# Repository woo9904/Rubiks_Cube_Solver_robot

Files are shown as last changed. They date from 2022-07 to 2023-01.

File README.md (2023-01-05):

# Rubiks Cube Solver Ver. 1.0 (RCSv1)

My first robot use Raspberry Pi 4 and Dynamixel_servo_motor(XM430-W350-T).   
It also detect 6 sides of the Rubiks_Cube and solving it with servo_motor.   
What i use algorithm is image precessing, motor control and python thread for LCD.   

In this code i modified cube detection algorithm, motor control and i added LCD.

임베디드장비(Raspberry Pi 4 B+)와 영상처리(큐브 인식), Dynamixel 제어를 스스로 공부해보고 활용해 큐브를 자동으로 맞춰주는 로봇을 만들었다.   
추가적으로 결과물 입출력을 확인하기 위해서 LCD패널 및 다양한 외부회로를 만들었다.   

* **제작자 : 정우진(Woo)**
* **제작 기간 : 22.02.28~22.05.15**
* **보고서 작성 일 : 22.05.25**

I reference this link. (Thank you Andrea Favero, Groningen(NL) for giving source.)
* [Reference_link](https://www.instructables.com/Rubik-Cube-Solver-Robot-With-Raspberry-Pi-and-Pica/)   

## Description

22년 5월 15일 최종적으로 1차 제작 완료한 모델로,
무작위로 섞은 큐브를 PiCam으로 인식하고, Dynamixel을 사용해 큐브를 푸는 로봇이다. 

큐브를 인식하고 푸는 시간은 총 3분 10초에서 3분 30초가 걸린다.   
빠른 로봇은 아니고, 이미 만들어진 제품을 참고한 작품이지만 스스로 배우고 학습하기에 적합한 활동이었다.  
이후 동아리 후배들이 작품을 봤을 때 자극을 받아 더 발전할 것이다.   
추후에는 더 발전시켜 완성도를 높일 것이다.

위 영상은 작동과정을 보여주고 있는 영상으로, 2배속을 한 영상이다.    
Video Label (https://youtu.be/7SincwjlR4I)

## Environment
실행에 필요한 package이다.   
* Hardware

로봇을 만드는데 사용한 부품에 대해 적는다.
|Raspberry Pi 4 Model B 4GB | Raspberry Pi Camera V2 | Dynamixel XM430-W350-T | U2D2 | GANCUBE | 
|--|--|--|--|--|
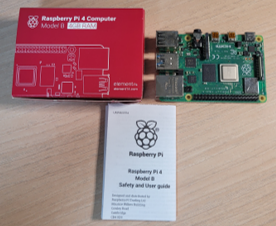
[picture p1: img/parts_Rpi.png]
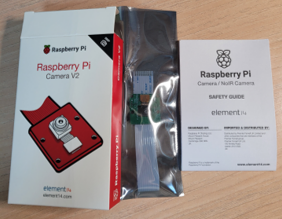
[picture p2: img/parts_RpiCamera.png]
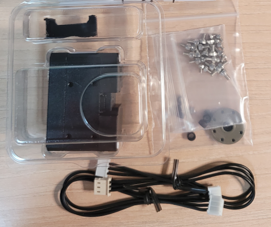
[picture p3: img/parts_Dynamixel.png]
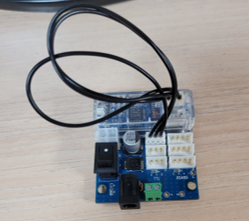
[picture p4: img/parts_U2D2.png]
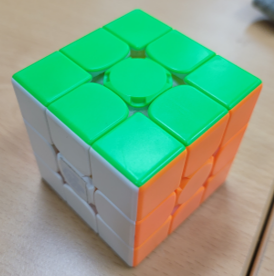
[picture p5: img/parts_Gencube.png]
||||||

* 3D models

각각 부품들을 조합해 나타낸 것이다. 세부 부품 설명은 추후에 적겠다. 
|3d model|출력 및 조립|
|---|---|
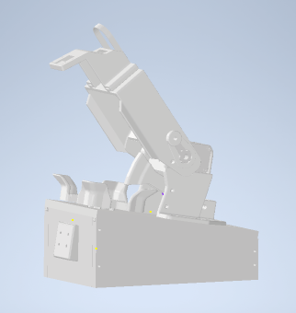
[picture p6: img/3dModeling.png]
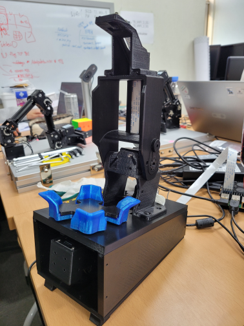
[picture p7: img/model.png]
|||

* Software

  * python 3.7.3, cv2 4.1.2
  * numpy, RPi.GPIO, PiCamera
  * twophase.solver (to install `$ pip install RubikTwoPhase`) 
  * Dynamixel_SDK (to install [link](https://emanual.robotis.com/docs/en/software/dynamixel/dynamixel_sdk/download/#repository))
  
## Files
작성한 코드가 각자 어떤 역할을 하는지 설명해준다. 
1. cube_detect_pi.py
    * 큐브 인식하기 위한 알고리즘
	* 이미지 프로세싱 포함
	
2. gpio_control.py
    * LCD화면, LED 등 외부 회로를 제어하기 위한 코드
	* 쓰레드를 사용함
	
3. main.py
    * 전체적인 코드를 통합한 코드
	* 각 코드를 연결하기 위한 코드이다. (main)
	
4. motor_control.py
    * 모터를 제어하기 위한 코드
	* 3개의 모터를 제어해 큐브를 돌린다.

추가적으로 motor제어에 안정화를 위해서 "Dynamixel_SDK"의 다음 라이브러리를 수정했다. 
-> 어떤 내용인지 작성하기

## Usage
작품을 실행하기 위한 방법에 대해 설명한다. 
1. Environment를 참고해 3d 모델을 뽑아 조립한다.
2. 그후 Hardware을 연결한다.
3. Software을 참고해 Raspberry Pi의 환경 세팅한다. 
4. git clone을 통해 CODE 부분을 Raspberry Pi에 저장한다. 
5. 명령창을 CODE의 폴더로 이동해 다음과 같이 명령어를 입력한다. 
```
$ python3 main.py
```
6. 그 후 외부 회로를 만들어 (회로도 참고) 버튼을 클릭해 실행한다. 
7. 만든 로봇을 통해 큐브를 맞춘다!

---------------------------------------------------------
## Story(a development journal)
개발 과정에 대해서 설명한다. 

### 개발 동기

필자는 임베디드 시스템을 한번도 경험해 보지 못했다. 이번 기회에 Raspberry Pi에 익숙해지고 경험을 쌓기로 했다.    
또한 모터 제어하는 방법을 잘 알지 못해 눈으로 로봇이 작동하는 것을 확인할 수 있으며 재미를 갖을 수 있는 요소를 찾다가   
'큐브 자동으로 맞춰주는 로봇'을 알게 되었다.    

또한 국민대 자율주행 자동차 대회 참가를 통해 처음 알게 된 image processing 기술을(본선진출) 좀더 이해하고 발전시켜 나가보기로 했다.   

따라서 다음과 같은 이유로 Cube solver을 제작하기로 했다. 

### 개발 목표

1) Picamera를 사용해 Cube 색깔 인식 알고리즘 구현   
2) 주어진 부품(Servo motor : Dynamixel)에 맞출 수 있는 로봇 하드웨어 modeling   
3) Dynamixel SDK를 참고해 모터 동작 알고리즘 구현   
4) 구현한 알고리즘과 하드웨어 결합으로 로봇 만들기   
5) LCD화면 및 스위치 장착   

## 작품 구성

로봇이 어떻게 구성되어 있는지 사진과 설명을 적는다. 또한 각 부품들이 어떤 역할을 하는지 설명한다.

### 작품 전체 사진

전체적인 작품 사진을 찍고 설명한다.
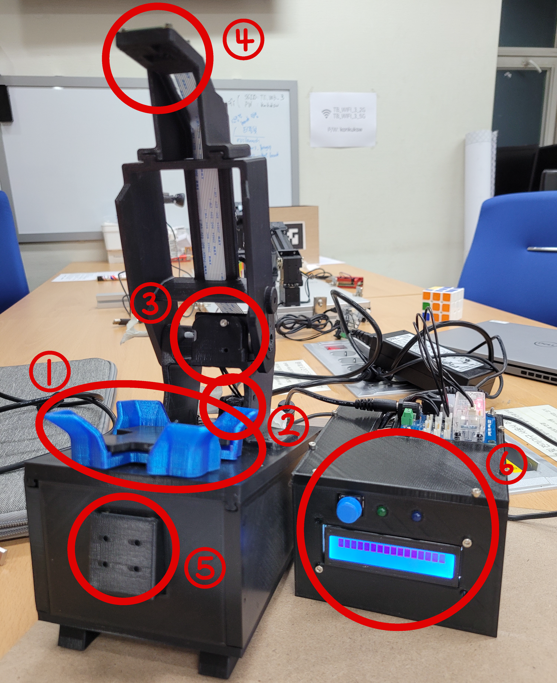
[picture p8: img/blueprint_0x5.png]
title

(시간 문제로 case부분 3d모델링을 하지 못해 임시적으로 사진을 다음과 같이 첨부했습니다.)

사용된 servo motor은 총 3개로 Robotis사의 Dynamixel XM430-W350-T모델을 사용했다.   
사용된 위치는 (1), (2), (3)이다.    

지면과 수평인 부분을 x축, 사진을 바라보고 있는 방향을 y축, 지면과 수직인 방향이 z축이라고 가정할 때,   
지면과 평면(xy축 평면)인 부분으로 회전시켜 주기 위해서 (1)번이 동작해야 하고,   
지면과 수직(yz축 평면)인 부분으로 회전시켜 주기 위해서는 (2)번이 동작해야 한다.   
큐브 면을 회전시키기 위해서는 큐브를 (3)모터로 고정시킨뒤 (1)번 모터를 동작시킨다.   

아래 사진은 2번 모터에서 shift가 동작해 큐브를 뒤집어 주는 모습이다.   
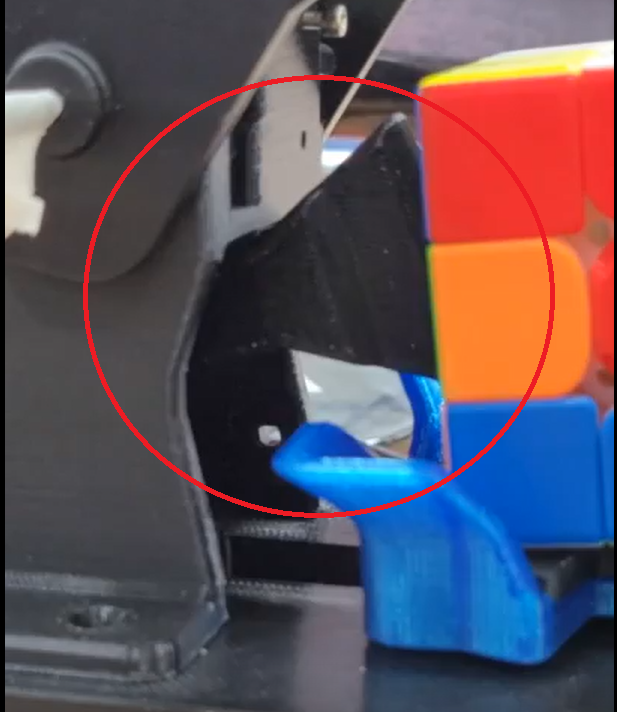
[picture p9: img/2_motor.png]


(4)번은 큐브면을 인식시켜 (color detect) 큐브 맞추는 solution을 제공하기 위해서 Rpi camera를 설치하였다.   
(5)번은 전체적으로 cube solver robot을 축소화 시키면서 발생한 부분이며, (1)번 모터를 고정시키기 위해서 필요한 motor holder이다.   
(6)번은 아직 case 완성품을 만들기 전이며, 외부 회로와 Raspberry pi를 보관하기 위한 case이다.   
motor를 크고 키기 위한 U2D2와 스위치는 보이는 곳에 두었다.   

* 동작 원리

전체적인 동작 원리는   
-> (6)번의 LCD화면을 통해 부팅이 성공적인지 확인 후, 스위치를 눌러 시작   
-> (4)번의 camera를 통해 cube의 6면의 색깔을 모두 인식 (이때 (1), (2), (3), 모터를 모두 사용해 큐브를 인식하기 위해 모터를 동작시킨다.)   
-> 인식된 색깔을 통해 cube solution을 계산하고 (1), (2), (3) 모터를 통해 큐브를 맞추기.   
-> 큐브를 모두 맞춘 경우, LCD화면에 성공 글자를 출력시키고, 다시 초기 상태로 복귀한다. 

### 사용한 부품

로봇을 만드는데 사용한 부품에 대해 적는다.
|Raspberry Pi 4 Model B 4GB | Raspberry Pi Camera V2 | Dynamixel XM430-W350-T | U2D2 | GANCUBE | 
|--|--|--|--|--|
|nn|nn|nn|nn|nn|

### 모델 parts
로봇을 만들기 위한 3D모델링에 대한 설명이다. 
아래 사진은 모델링을 하기 위해 참고한 모델들이다. 

|1번|2번|3번|
|--|--|--|
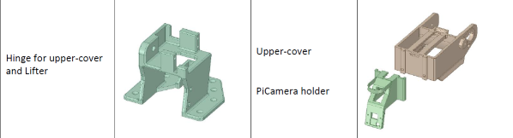
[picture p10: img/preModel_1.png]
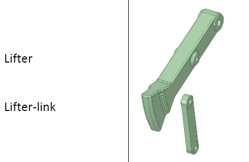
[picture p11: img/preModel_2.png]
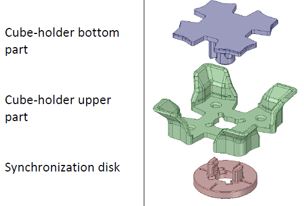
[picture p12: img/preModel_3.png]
||||

하지만 아래 사진 처럼 주어진 모델이 사용하고자 하는 servo motor에 맞지 않았다. 

|1번|2번|3번|
|---|---|---|
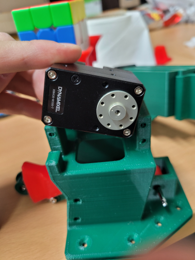
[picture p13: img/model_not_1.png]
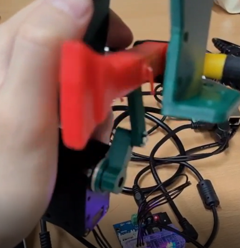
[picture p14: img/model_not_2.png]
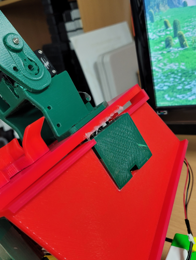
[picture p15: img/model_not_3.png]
||||
|기본 모델이 servo motor 크기와 부합. |Lifter 부분이 motor과 다른 설계로 cube를 뒤집지 못함. | motor을 holder 부분이 없어 부품 조립에 문제. |

3D 모델링으로 모든 모델링을 수정하고 제작해 다음과 같은 모델을 만들 수 있게 되었다. 

|3d model|출력 및 조립|
|---|---|
|nn|nn|

## 작동 알고리즘

로봇이 큐브를 인식하기 부터 풀기까지 모든 동작의 알고리즘에 대해 설명한다. 

### 배경지식

해당 로봇과 관련된 선행 조사에 대해 작성한다.
사용한 큐브   

|western_cube|cube_table|
|--|--|
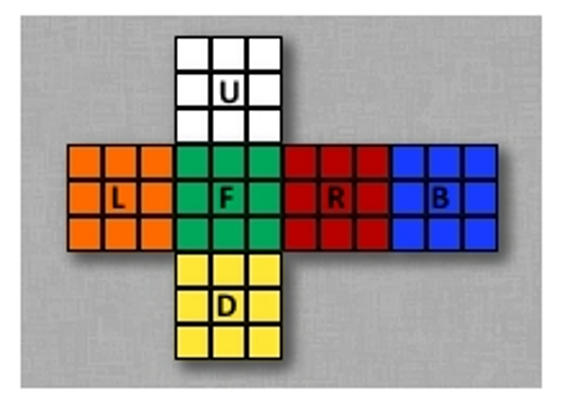
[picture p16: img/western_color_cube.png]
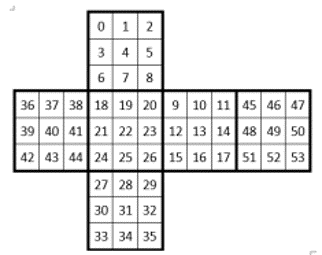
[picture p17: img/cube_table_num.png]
|||

 큐브 설명하기
|큐브 돌릴때 사용하는 명칭| 큐브 맞추는 방법 알고리즘|
|--|--|
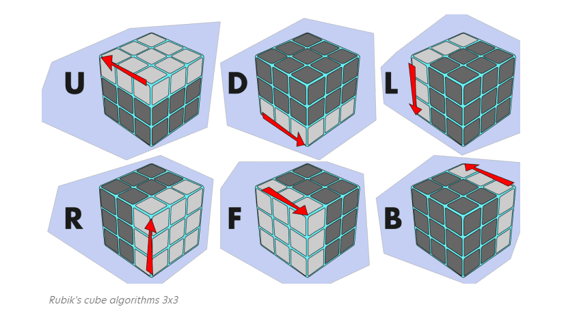
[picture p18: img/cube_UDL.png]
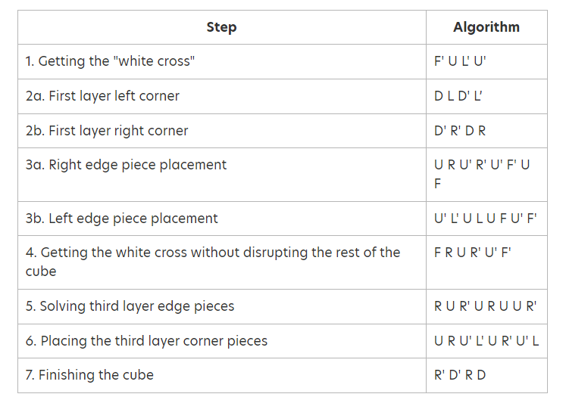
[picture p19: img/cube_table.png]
|||

 Raspberry Pi의 GPIO

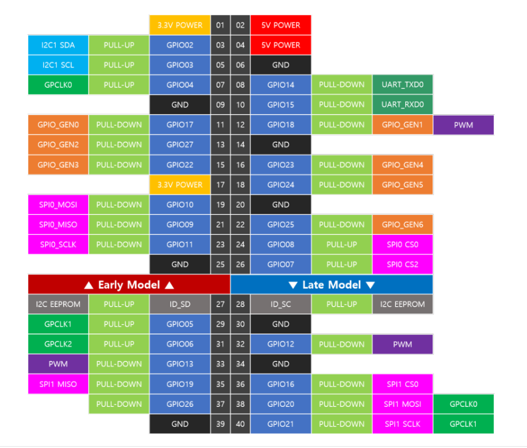
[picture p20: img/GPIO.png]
   

### 사용한 기술

일을 수행하기 위한 사용한 알고리즘 및 기법에 대해 작성한다.

1. OpenCV, cube face contour detect

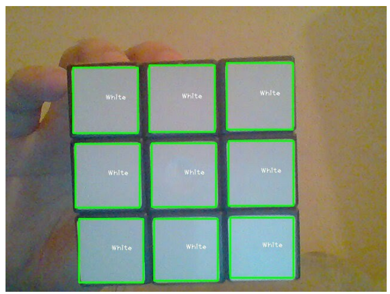
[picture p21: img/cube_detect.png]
   

2. color recognize using HSV

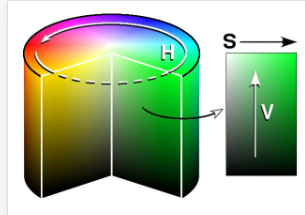
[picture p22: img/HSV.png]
   

3. Dynamixel SDK

## 개발 과정

개발하면서 크게 어려웠던 점을 순서대로 나열하고 해결방법은 아래에 작성한다.

### 하드웨어 개발 과정

### 소프트웨어 개발 과정

#### 영상처리

#### 모터제어

## 추후 목표

## 결론

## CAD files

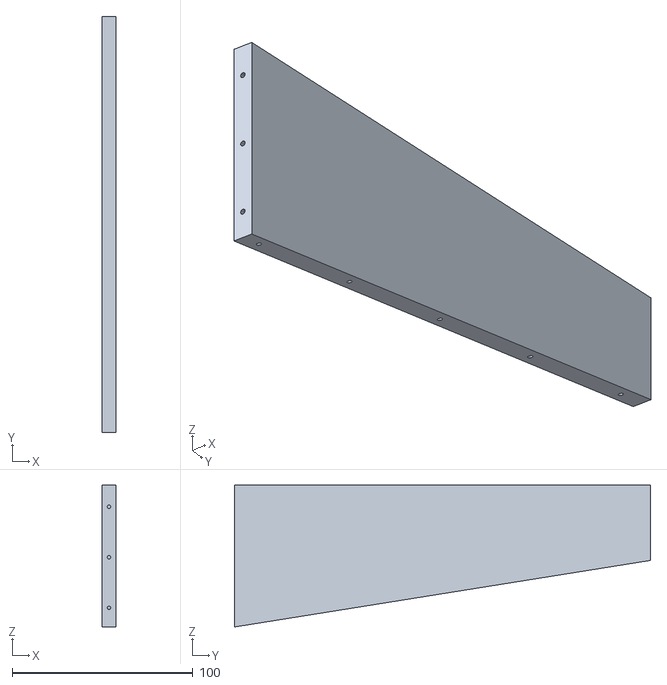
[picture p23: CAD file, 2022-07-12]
3D_model/stl_for_model/Panel_left.stl
8.00 x 230.0 x 78.5

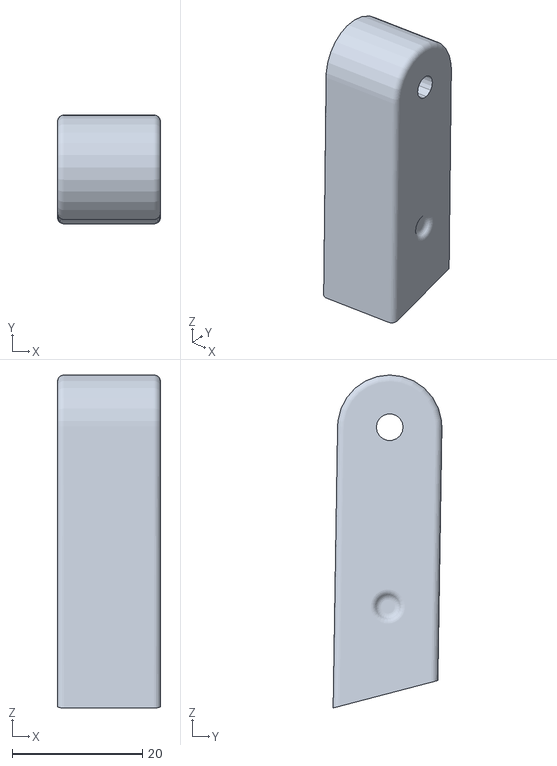
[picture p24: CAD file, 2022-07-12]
3D_model/stl_for_model/Foot.stl
15.8 x 16.7 x 51.0

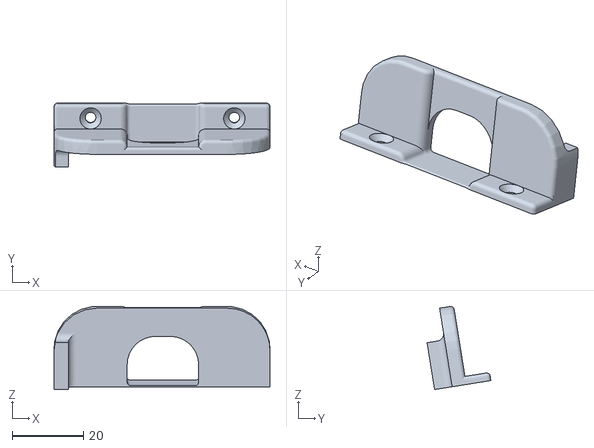
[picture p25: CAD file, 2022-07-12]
3D_model/stl_for_model/Rpi_holder_back.stl
60.5 x 17.9 x 23.3

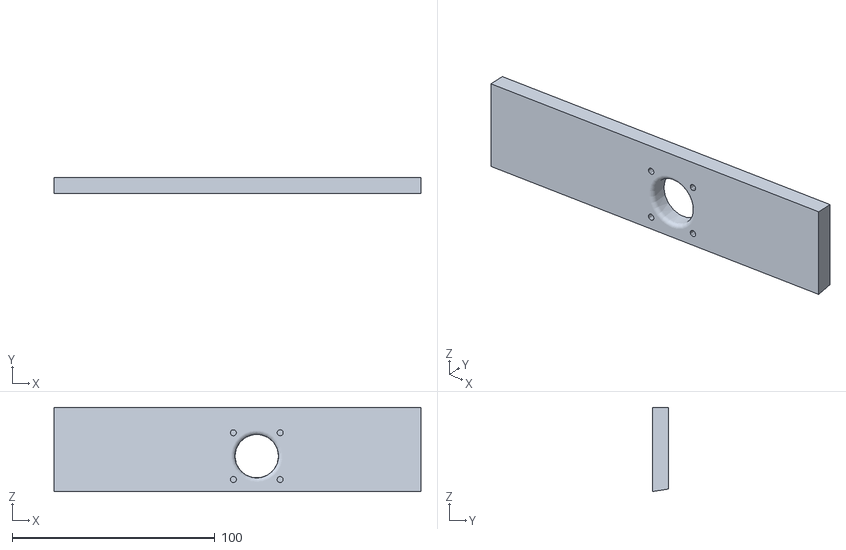
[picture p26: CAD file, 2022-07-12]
3D_model/stl_for_model/Panel_back.stl
181.0 x 8.00 x 41.5

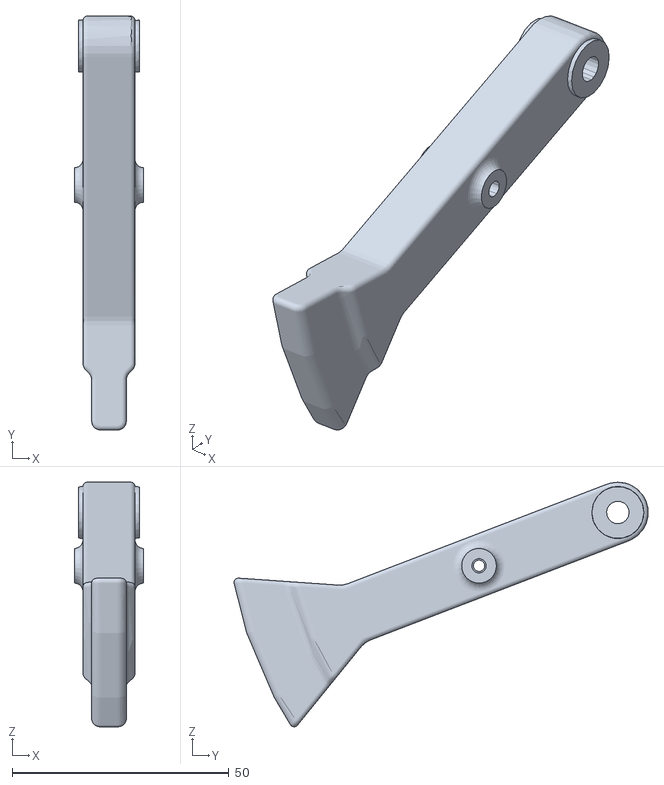
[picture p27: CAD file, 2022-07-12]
3D_model/stl_for_model/Lifter.stl
16.0 x 95.5 x 56.4

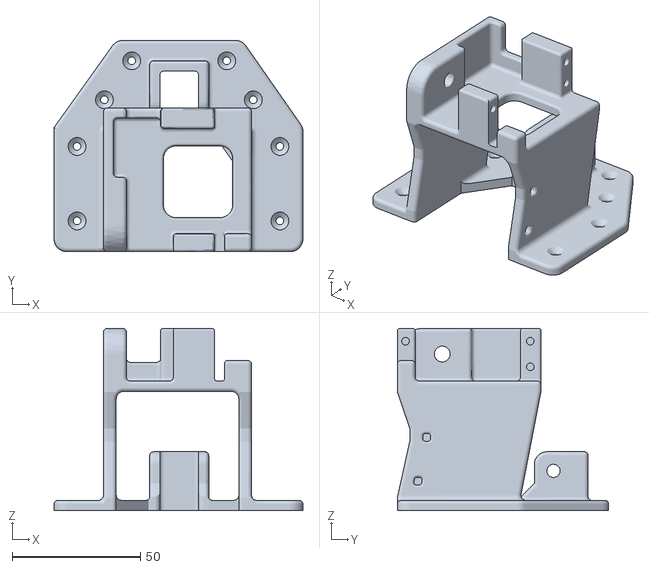
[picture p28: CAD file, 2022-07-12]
3D_model/stl_for_model/Hinge_upperCover_Lifter.stl
97.0 x 82.4 x 71.0

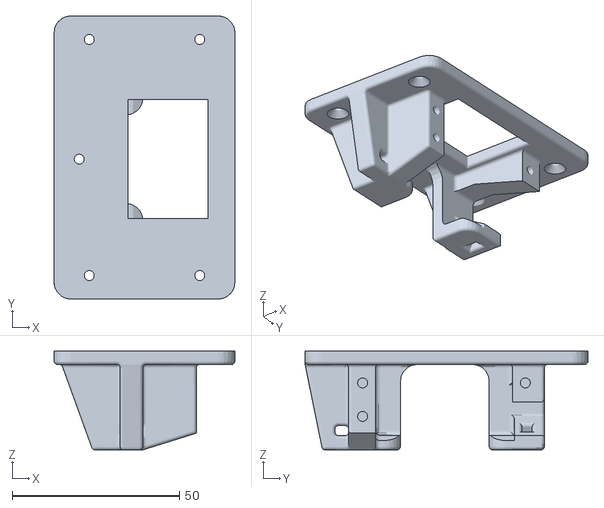
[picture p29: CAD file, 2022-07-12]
3D_model/stl_for_model/Lifter_servo_holder.stl
54.0 x 84.5 x 29.5

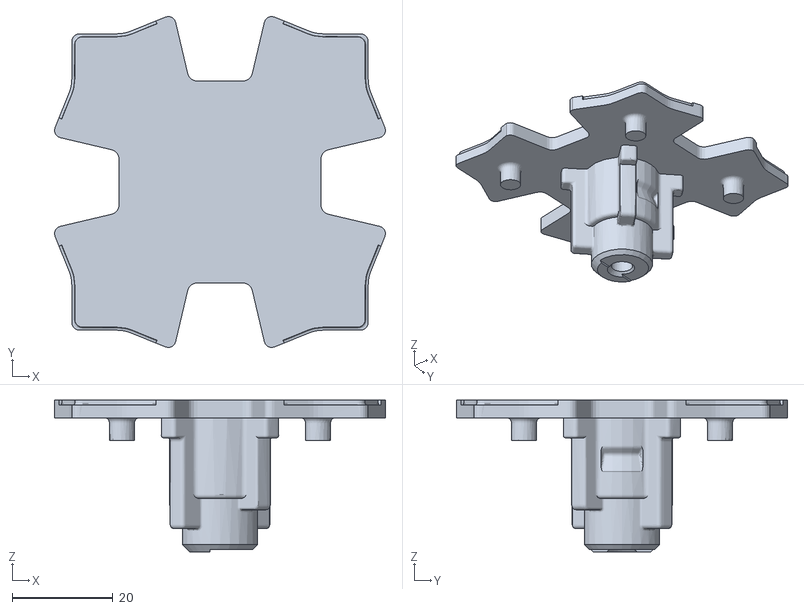
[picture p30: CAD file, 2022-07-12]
3D_model/stl_for_model/Cube_holder_lower_part.stl
65.7 x 65.7 x 30.1

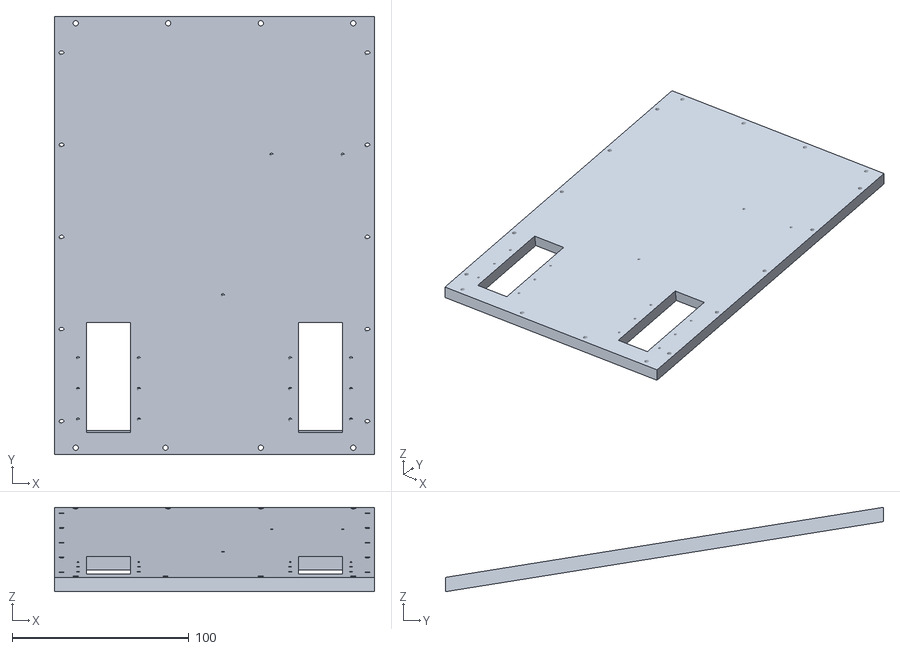
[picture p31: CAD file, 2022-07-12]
3D_model/stl_for_model/Panel_bottom.stl
181.0 x 248.0 x 47.8

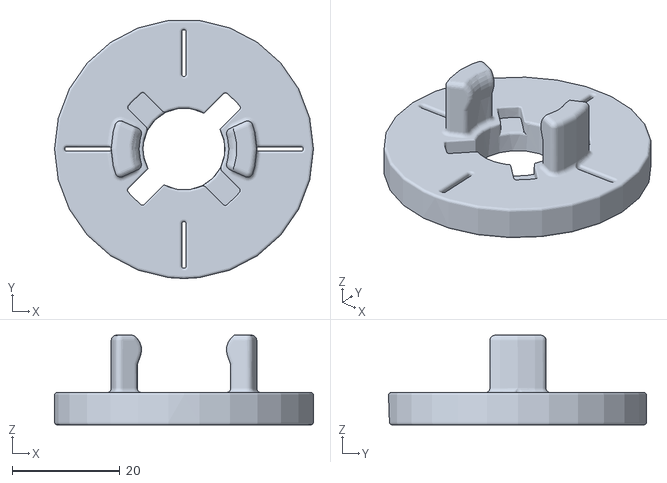
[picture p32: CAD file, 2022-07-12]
3D_model/stl_for_model/Motor_sync_disk.stl
48.0 x 47.8 x 16.6

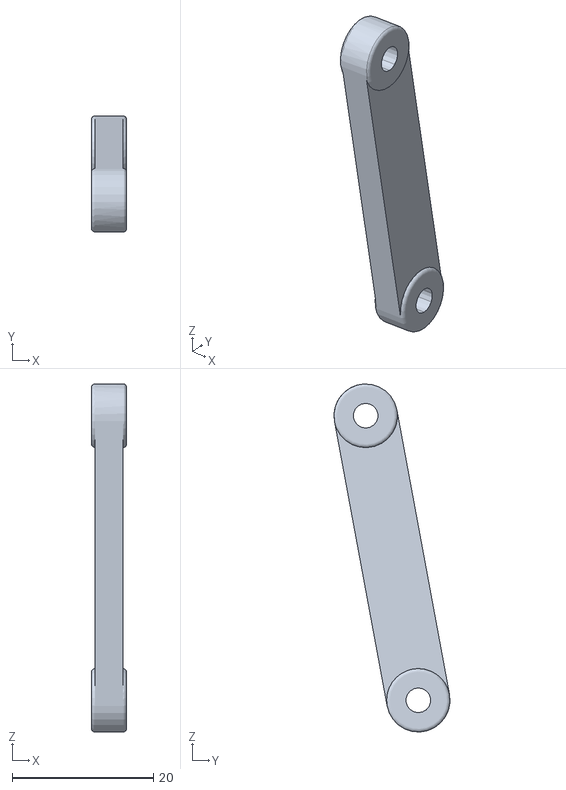
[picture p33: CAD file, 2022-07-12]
3D_model/stl_for_model/Lever_link.stl
5.00 x 16.4 x 49.3

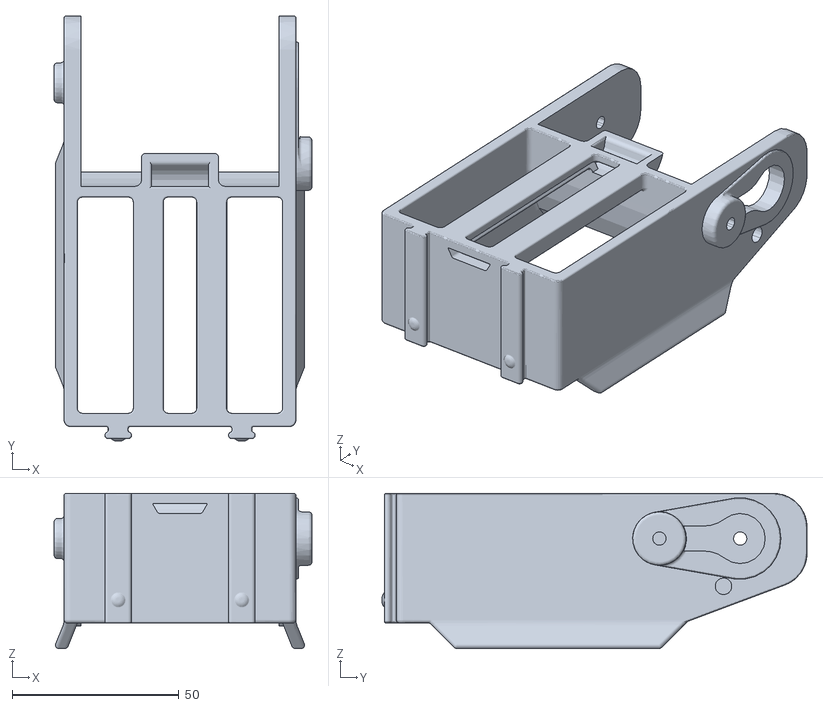
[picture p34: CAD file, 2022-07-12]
3D_model/stl_for_model/Upper_cover.stl
77.2 x 127.3 x 46.4

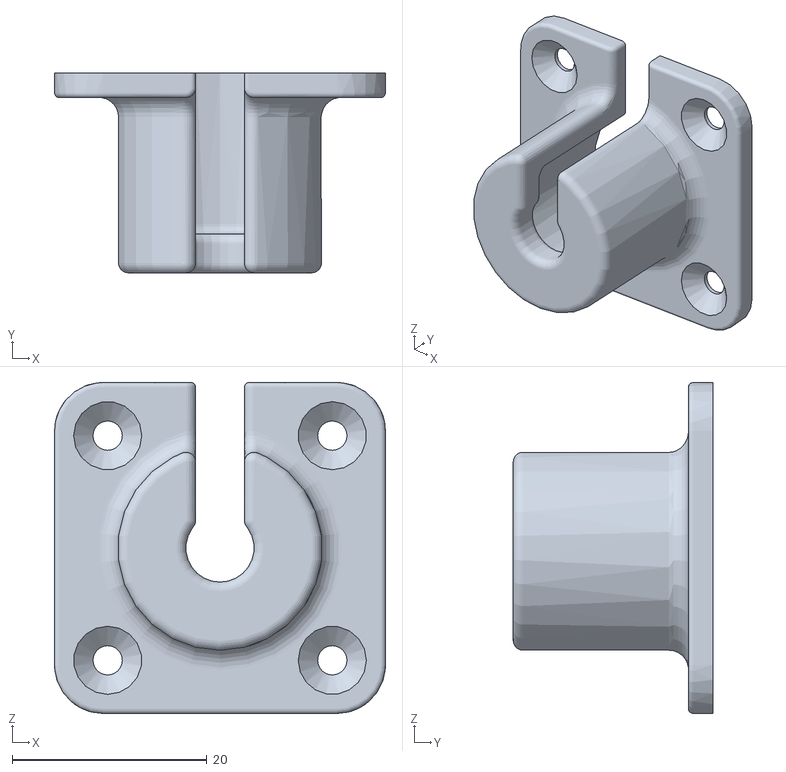
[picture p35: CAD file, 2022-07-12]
3D_model/stl_for_model/Power_connector_inner_part.stl
34.0 x 20.5 x 34.0

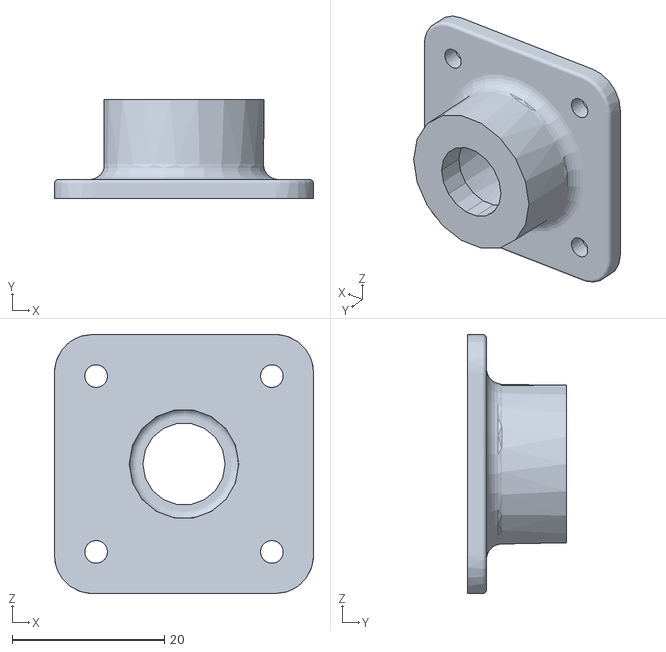
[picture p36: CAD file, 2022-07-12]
3D_model/stl_for_model/Power_connector_outer_part.stl
34.0 x 13.0 x 34.0

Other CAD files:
3D_model/stl_for_model/Panel_front.stl
3D_model/stl_for_model/Rpi_holder_front.stl
3D_model/stl_for_model/Panel_top.stl
3D_model/stl_for_model/Panel_right.stl
3D_model/stl_for_model/Foot_hinge.stl

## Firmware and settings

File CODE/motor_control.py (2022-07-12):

#!/usr/bin/env python
# -*- coding: utf-8 -*-

#--------------------------
#모터를 제어하기 위해서 만든 함수
#---------------------------
import os
from dynamixel_sdk import *                    # Uses Dynamixel SDK library
import time

flag=0
cycle=10
correction=0

#포트 열기
def open_port():
    global packetHandler, portHandler, ADDR_TORQUE_ENABLE, ADDR_GOAL_POSITION,TORQUE_DISABLE, TORQUE_ENABLE, getch, ADDR_PRESENT_POSITION, DXL_MOVING_STATUS_THRESHOLD
    if os.name == 'nt':
        import msvcrt
        def getch():
            return msvcrt.getch().decode()
    else:
        import sys, tty, termios
        fd = sys.stdin.fileno()
        old_settings = termios.tcgetattr(fd)
        def getch():
            try:
                tty.setraw(sys.stdin.fileno())
                ch = sys.stdin.read(1)
            finally:
                termios.tcsetattr(fd, termios.TCSADRAIN, old_settings)
            return ch

    MY_DXL = 'X_SERIES'       # X330 (5.0 V recommended), X430, X540, 2X430
    ADDR_TORQUE_ENABLE          = 64
    ADDR_GOAL_POSITION          = 116
    ADDR_PRESENT_POSITION       = 132
    DXL_MINIMUM_POSITION_VALUE  = 0         # Refer to the Minimum Position Limit of product eManual
    DXL_MAXIMUM_POSITION_VALUE  = 4095      # Refer to the Maximum Position Limit of product eManual
    BAUDRATE                    = 115200

    PROTOCOL_VERSION            = 2.0

    DEVICENAME                  = '/dev/ttyUSB0'
    TORQUE_ENABLE               = 1                 # Value for enabling the torque
    TORQUE_DISABLE              = 0                 # Value for disabling the torque
    DXL_MOVING_STATUS_THRESHOLD = 10                # Dynamixel moving status threshold

    portHandler = PortHandler(DEVICENAME)
    packetHandler = PacketHandler(PROTOCOL_VERSION)

    # Open port
    if portHandler.openPort():
        print("Succeeded to open the port")
    else:
        print("Failed to open the port")
        print("Press any key to terminate...")
        getch()
        quit()

    # Set port baudrate
    if portHandler.setBaudRate(BAUDRATE):
        print("Succeeded to change the baudrate")
    else:
        print("Failed to change the baudrate")
        print("Press any key to terminate...")
        getch()
        quit()

#모터 동작시키기
def motor_move(motor_id, dir ,times):
    global packetHandler, portHandler
    #1번 모터 동작
    if motor_id==1:
        DXL1_ID = 1                 # Dynamixel#1 ID : 1

        cycle=times #1번 모터가 한바퀴를 넘길때 늘어남
        flag=dir
        dxl_goal_position_1 = [930, 1954, 2978, 4002]

        # Enable Dynamixel#1 Torque
        dxl_comm_result, dxl_error = packetHandler.write1ByteTxRx(portHandler, DXL1_ID, ADDR_TORQUE_ENABLE, TORQUE_ENABLE)
        if dxl_comm_result != COMM_SUCCESS:
            print("%s" % packetHandler.getTxRxResult(dxl_comm_result))
        elif dxl_error != 0:
            print("%s" % packetHandler.getRxPacketError(dxl_error))
        else:
            print("Dynamixel#%d has been successfully connected" % DXL1_ID)

        
        #write goal position
        dxl_comm_result, dxl_error = packetHandler.write4ByteTxRx(portHandler, DXL1_ID, ADDR_GOAL_POSITION, dxl_goal_position_1[flag]+cycle*4096+correction)
        print(flag, cycle, correction)
        
        if dxl_comm_result != COMM_SUCCESS:
            print("%s" % packetHandler.getTxRxResult(dxl_comm_result))
        elif dxl_error != 0:
            print("%s" % packetHandler.getRxPacketError(dxl_error))


        while 1:
            dxl1_present_position, dxl_comm_result, dxl_error = packetHandler.read4ByteTxRx(portHandler, DXL1_ID, ADDR_PRESENT_POSITION)
            if dxl_comm_result != COMM_SUCCESS:
                print("%s" % packetHandler.getTxRxResult(dxl_comm_result))
            elif dxl_error != 0:
                print("%s" % packetHandler.getRxPacketError(dxl_error))

            if not ((abs(dxl_goal_position_1[flag]+cycle*4096+correction - dxl1_present_position) > DXL_MOVING_STATUS_THRESHOLD)):
                break

        # Disable Dynamixel#1 Torque
        dxl_comm_result, dxl_error = packetHandler.write1ByteTxRx(portHandler, DXL1_ID, ADDR_TORQUE_ENABLE, TORQUE_DISABLE)
        if dxl_comm_result != COMM_SUCCESS:
            print("%s" % packetHandler.getTxRxResult(dxl_comm_result))
        elif dxl_error != 0:
            print("%s" % packetHandler.getRxPacketError(dxl_error))

    #2번 모터 동작
    if motor_id==2:
        DXL2_ID = 2                 # Dynamixel#2 ID : 2

        cycle_2=times #2번 모터가 한바퀴를 넘길때 늘어남
        dxl_goal_position_2 = 4096

        # Enable Dynamixel#2 Torque
        dxl_comm_result, dxl_error = packetHandler.write1ByteTxRx(portHandler, DXL2_ID, ADDR_TORQUE_ENABLE, TORQUE_ENABLE)
        if dxl_comm_result != COMM_SUCCESS:
            print("%s" % packetHandler.getTxRxResult(dxl_comm_result))
        elif dxl_error != 0:
            print("%s" % packetHandler.getRxPacketError(dxl_error))
        else:
            print("Dynamixel#%d has been successfully connected" % DXL2_ID)

        # Write goal position
        dxl_comm_result, dxl_error = packetHandler.write4ByteTxRx(portHandler, DXL2_ID, ADDR_GOAL_POSITION, dxl_goal_position_2*cycle_2)
        if dxl_comm_result != COMM_SUCCESS:
            print("%s" % packetHandler.getTxRxResult(dxl_comm_result))
        elif dxl_error != 0:
            print("%s" % packetHandler.getRxPacketError(dxl_error))

        while 1:
            # Syncread present position
            #time.sleep(0.01)
            dxl2_present_position, dxl_comm_result, dxl_error = packetHandler.read4ByteTxRx(portHandler, DXL2_ID, ADDR_PRESENT_POSITION)
            if dxl_comm_result != COMM_SUCCESS:
                print("%s" % packetHandler.getTxRxResult(dxl_comm_result))
            elif dxl_error != 0:
                print("%s" % packetHandler.getRxPacketError(dxl_error))

            #print("[ID:%03d] GoalPos:%03d  PresPos:%03d" % (DXL2_ID, dxl_goal_position_2*cycle_2, dxl2_present_position))

            if not ((abs(dxl_goal_position_2*cycle_2 - dxl2_present_position) > DXL_MOVING_STATUS_THRESHOLD)):
                #time.sleep(0.1)
                break

        # Disable Dynamixel#2 Torque
        dxl_comm_result, dxl_error = packetHandler.write1ByteTxRx(portHandler, DXL2_ID, ADDR_TORQUE_ENABLE, TORQUE_DISABLE)
        if dxl_comm_result != COMM_SUCCESS:
            print("%s" % packetHandler.getTxRxResult(dxl_comm_result))
        elif dxl_error != 0:
            print("%s" % packetHandler.getRxPacketError(dxl_error))
            
    #3번 모터 동작
    if motor_id==3:
        DXL3_ID = 3                 # Dynamixel#3 ID : 3

        index_3=dir
        dxl_goal_position_3 = [400, 1200]

        # Enable Dynamixel#3 Torque
        dxl_comm_result, dxl_error = packetHandler.write1ByteTxRx(portHandler, DXL3_ID, ADDR_TORQUE_ENABLE, TORQUE_ENABLE)
        if dxl_comm_result != COMM_SUCCESS:
            print("%s" % packetHandler.getTxRxResult(dxl_comm_result))
        elif dxl_error != 0:
            print("%s" % packetHandler.getRxPacketError(dxl_error))
        else:
            print("Dynamixel#%d has been successfully connected" % DXL3_ID)

        #write goal position
        dxl_comm_result, dxl_error = packetHandler.write4ByteTxRx(portHandler, DXL3_ID, ADDR_GOAL_POSITION, dxl_goal_position_3[index_3])

        if dxl_comm_result != COMM_SUCCESS:
            print("%s" % packetHandler.getTxRxResult(dxl_comm_result))
        elif dxl_error != 0:
            print("%s" % packetHandler.getRxPacketError(dxl_error))

        while 1:
            dxl3_present_position, dxl_comm_result, dxl_error = packetHandler.read4ByteTxRx(portHandler, DXL3_ID, ADDR_PRESENT_POSITION)
            if dxl_comm_result != COMM_SUCCESS:
                print("%s" % packetHandler.getTxRxResult(dxl_comm_result))
            elif dxl_error != 0:
                print("%s" % packetHandler.getRxPacketError(dxl_error))

            if not ((abs(dxl_goal_position_3[index_3] - dxl3_present_position) > DXL_MOVING_STATUS_THRESHOLD)):
                break

        # Disable Dynamixel#3 Torque
        #dxl_comm_result, dxl_error = packetHandler.write1ByteTxRx(portHandler, DXL3_ID, ADDR_TORQUE_ENABLE, TORQUE_DISABLE)
        #if dxl_comm_result != COMM_SUCCESS:
            #print("%s" % packetHandler.getTxRxResult(dxl_comm_result))
        #elif dxl_error != 0:
            #print("%s" % packetHandler.getRxPacketError(dxl_error))

#모터 초기화 시키기
def motor_initial():
    global flag, cycle, index, cycle_2
    flag=0
    cycle=10
    motor_move(1, flag, cycle)

    index=1
    motor_move(3, index, index)
    
    time.sleep(1)

    cycle_2=5
    motor_move(2, cycle_2, cycle_2)

#1번 모터 동작시키기 wrapper
def motor_1(dir, times):
    global flag, cycle, correction
    if dir=="+":
        flag+=times
    elif dir=="-":
        flag-=times

    if flag>=4:
        flag=flag-4
        cycle+=1
    elif flag<0:
        flag=flag+4
        cycle-=1

    if index==0:
        correction=150
        if dir=="-":
            correction=-150
        
        motor_move(1, flag, cycle) #1번 모터, flag 인덱스만큼, cycle횟수만큼
        correction=0
        motor_move(3, 1, 1) #3 motor Up,
        time.sleep(0.1)
        motor_move(1, flag, cycle) #1번 모터, flag 인덱스만큼, cycle횟수만큼
    else:
        correction=0
        motor_move(1, flag, cycle) #1번 모터, flag 인덱스만큼, cycle횟수만큼

#2번 모터 동작시키기 wrapper
def motor_2(dir, times):
    global cycle_2
    if dir=="+":
        cycle_2+=times
    elif dir=="-":
        cycle_2-=times

    motor_move(2, cycle_2, cycle_2)

#3번 모터 동작시키기 wrapper
def motor_3(dir):
    global index
    if dir=="U":
        if index==1:
            return
        else:
            index=1
    elif dir=="D":
        if index==0:
            return
        else:
            index=0

    motor_move(3, index, index)

#총 모터 동작
def robot_move_s(input_msg):
    global flag, do_dir_opposite
    do_it=input_msg[0]
    num=int(input_msg[1])
    do_dir_opposite=False

    # 3회인 경우 돌리는 방향 반대
    if num==3:
        do_dir_opposite=True
        num=1

    #U는 뒤집으면 반대방향임. 
    if do_it=="U":
        motor_3("U")
        time.sleep(0.1)
        motor_2("+", 2)
        time.sleep(0.1)
        motor_3("D")

        if do_dir_opposite==True: #방향 반대
            input_dir="+"
        else: #방향 그대로
            input_dir="-"
        motor_1(input_dir, num)

        #초기상태 복귀
        motor_3("U")
        time.sleep(0.5)
        motor_2("-", 2)
    elif do_it=="D":
        motor_3("D")
        if do_dir_opposite==True:
            input_dir="+"
        else:
            input_dir="-"
        motor_1(input_dir, num)

        #초기상태 복귀
        motor_3("U")
    elif do_it=="L":
        motor_3("U")
        motor_1("+", 1)
        time.sleep(0.1)
        motor_2("+", 1)
        time.sleep(0.1)
        motor_3("D")
        if do_dir_opposite==True: #방향 반대
            input_dir="+"
        else: #방향 그대로
            input_dir="-"
        motor_1(input_dir, num)

        #초기상태 복귀
        motor_3("U")
        time.sleep(0.5)
        motor_2("-", 3)
        time.sleep(0.1)
        motor_1("-", 1)
    elif do_it=="R":
        motor_3("U")
        motor_1("-", 1)
        motor_2("-", 1)
        motor_3("D")
        if do_dir_opposite==True: #방향 반대
            input_dir="+"
        else: #방향 그대로
            input_dir="-"
        time.sleep(0.1)
        motor_1(input_dir, num)

        #초기상태
        motor_3("U")
        time.sleep(0.5)
        motor_2("+", 3)
        time.sleep(0.1)
        motor_1("+", 1)
    elif do_it=="F":
        motor_3("U")
        time.sleep(0.1)
        motor_2("+", 3)
        time.sleep(0.1)
        motor_3("D")
        if do_dir_opposite==True: #방향 반대
            input_dir="+"
        else: #방향 그대로
            input_dir="-"
        time.sleep(0.1)
        motor_1(input_dir, num)

        #초기
        motor_3("U")
        time.sleep(0.1)
        motor_2("-", 1)
    elif do_it=="B":
        motor_3("U")
        time.sleep(0.1)
        motor_2("+", 1)
        time.sleep(0.1)
        motor_3("D")
        if do_dir_opposite==True: #방향 반대
            input_dir="+"
        else: #방향 그대로
            input_dir="-"
        time.sleep(0.1)
        motor_1(input_dir, num)

        #초기
        motor_3("U")
        time.sleep(0.5)
        motor_2("-", 3)
        time.sleep(0.1)



#포트 종료
def close_port():
    # Close port
    portHandler.closePort()


if __name__=="__main__":
    open_port()
    motor_initial()
    close_port()

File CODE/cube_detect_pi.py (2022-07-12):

#!/usr/bin/env python
# coding: utf-8


""" 
#############################################################################################################
#  Andrea Favero
#
#  While dealing with Covid 19 pandemic on 2021, and turning 50 years old, I thought a Rubik's cube
#  solver robot to be a nice challenge, to learn computer vision and to improve my coding skills.
#
#  The below code works on a PC (presenting the cube faces manually to the webcam) and/or on a raspberry pi.
#  I've used the Kociemba solveimr (from: https://github.com/hkociemba/RubiksCube-TwophaseSolver)
#
#  The Rpi part integrates the controls for a robot I've develloped.
#  It shouldn't be too difficult to comment out the robot related parts, and just use the Rpi + camera;
#  This will allow to read the cube status via the Vision part, and to retrieve the cube solution.
#
#
#  Developped on:
#  --> W10 PC with Python ver: 3.8.12 [MSC v.1916 64 bit (AMD64)] and cv2 ver: 4.5.1
#  --> Raspberry pi 4B 2Gb piCamera v1.3, with Python version: 3.7.3 and cv2 ver: 4.1.0
#
#  Verified on:
#  --> W10 PC with Python ver: 3.9.7 |packaged by conda-forge| [MSC v.1916 64 bit (AMD64)] and cv2 ver: 4.5.1
#
#############################################################################################################
"""


import cv2
from cv2 import imshow
import numpy as np
from copy import deepcopy
from scipy.misc import face
from scipy.spatial import distance as dist
import math
import statistics
import time
import datetime as dt
import sys
import motor_control





def webcam():
    #카메라 영상, 너비, 높이 
    """ Set the camera and its resolution"""
    global camera
    
    #if device == 'laptop':
    s_mode = 6                             # sensor mode 7 means 4x4 binning
    camera = PiCamera(sensor_mode=s_mode)  # PiCamera is set as camera object
    rawCapture = PiRGBArray(camera)        # returns (uncoded) RGB array from the camera
        
    # necessary to use a large FOW (Field of view) as the camera is rather close to the cube
    camera_width_resolution = 1088         # PiCamera width resolution setting
    camera_hight_resolution = 720          # PiCamera height resolution setting
    width = camera_width_resolution            
    height =  camera_hight_resolution
    camera.resolution = (width, height)    # camera's resolution is set
        
    binning = camera.sensor_mode           # PiCamera sensor_mode is checked
        
    # sensor_mode answer from the camera is interpreted
    if binning <=3:
        binning='none'
    elif binning == 4 or binning == 5:
        binning='2x2'
    elif binning > 5:
        binning='4x4'
            
    if side==0:                     # only at cube reading start the camera's resolution in print at terminal
        print(f'PiCamera resolution: {width} x {height},   binning: {binning}\n')
        time.sleep(0.2)
#   clear_terminal(device)
    return camera, rawCapture, width, height
    
    

def robot_camera_warmup():
    """
    According to PiCamera documentation it is required a couple of seconds to warmup the camera.
    If the robot start-button is pressed right after placing the cube, the camera has to update the gains set before,
    that means from when tha camera was pointing the black cube support; this can take up to 20 secs to get all
    the gains stable (awb gains are rather slow to update).
    Much different is when the cube is on the cube support for few secs when the button is pressed.
    To properly cover all the possible situations, this fuction releases the camera warm-up phase only after
    aLL the gains are stable, meaning an absolute variation < 2% from the average of last 2 seconds.
    """    
    #if device=='Rpi' and robot_stop==False:
    if device=='Rpi':
        camera.exposure_mode = 'auto' # set to auto exposure at the start, to adjust according to light conditions
        camera.awb_mode = 'auto'      # set to auto white balance at the start, to adjust according to light conditions
        time.sleep(0.2)               # not found documentation if a delay is needed after this PiCamera setting 
        a_gain_list=[]                # list to store the Picamera analog gain, during warmup period
        d_gain_list=[]                # list to store the Picamera digital gain, during warmup period
        awb_blue_list=[]              # list to store the Picamera AWB gain, for blue, during warmup period
        awb_red_list=[]               # list to store the Picamera AWB gain, for red, during warmup period
        t_list=[]                     # list to store the warmup progressive time of checkings
        
        kl=0.98                       # lower koefficient to define acceptance bandwidth (98%)
        ku=2-kl                       # Upper koefficient to define acceptance bandwidth (102%)
        if screen:
            pts=12                    # amount of consecutive datapoints to analyse if within acceptable range
                                      # few points less than no screen as the system is slower
        else:
            pts=14                    # amount of consecutive datapoints to analyse if within acceptable range
        
        t_start=time.time()        # time reference is allocated as reference for the next task
        
        while time.time()-t_start <20:                               # timeout for camera warm-up phase is 20 seconds
            frame, w, h = pre_read_camera()                             # camera start reading the cube, and adjusts the awb/exposure
            a_gain_list.append(round(float(camera.analog_gain),2))      # analog gain is appended to a list
            d_gain_list.append(round(float(camera.digital_gain),2))     # digital gain is appended to a list
            awb_blue_list.append(round(float(camera.awb_gains[0]),2))   # awb blue part gain is appended to a list
            awb_red_list.append(round(float(camera.awb_gains[1]),2))    # awb blue part gain is appended to a list
            t_list.append(round(time.time()- t_start,2))              # time (from AWB and Exposition start adjustement) is appended to a list
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

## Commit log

2022-07-12 first update
    [Cube_holder_lower_part.stl, Foot.stl, Foot_hinge.stl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]
2022-07-13 modify 3Dmodel
    [Cube_holder_lower_part.stl, Foot.stl, Foot_hinge.stl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]
2022-07-13 3Dmodels added
    [Cube_holder_lower_part.stl, Foot.stl, Foot_hinge.stl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]
